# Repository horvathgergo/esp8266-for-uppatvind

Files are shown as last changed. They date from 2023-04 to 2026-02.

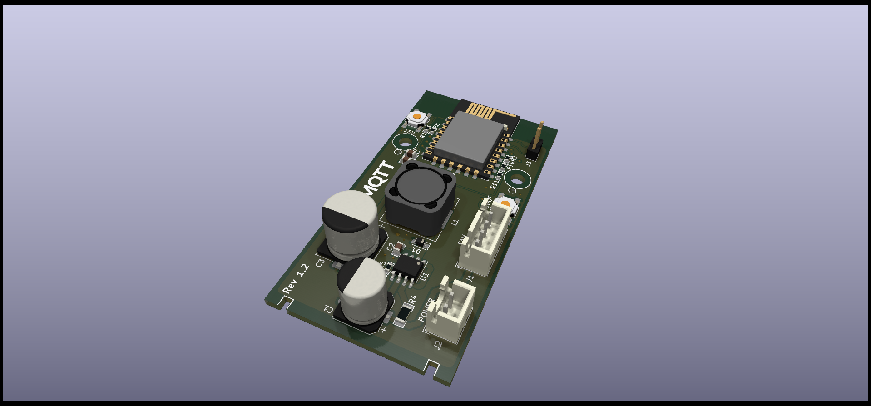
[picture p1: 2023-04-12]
Hardware/3D-model/3d-front2.png

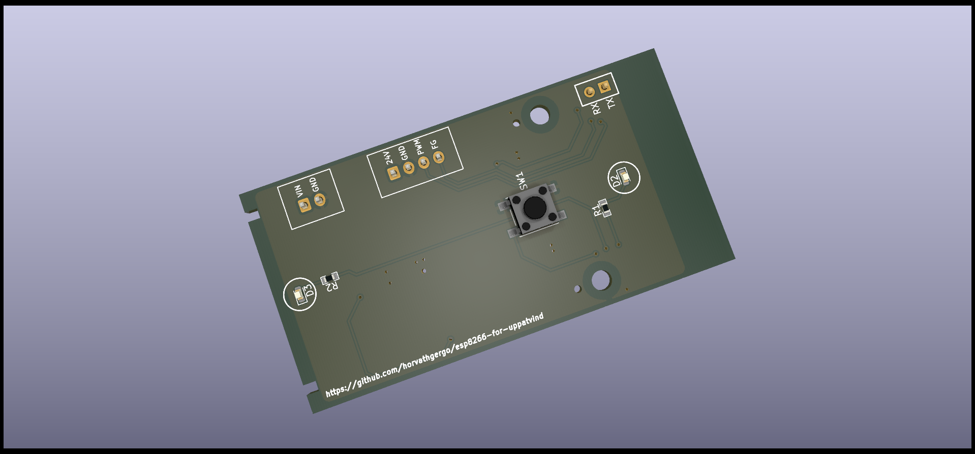
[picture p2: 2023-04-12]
Hardware/3D-model/3d-back.png

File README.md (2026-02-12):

# Smart Air Purifier (Project Uppåtvind)
Custom PCB based on ESP12-F (ESP8266) wifi module that serves as a smart controller for IKEA Uppåtvind Air Purifiers. It's embedded microcontroller enables you to incorporate your device to home automation systems (preferably to Home Assistant) or control it via custom mobile applications as it enjoys support from wide variety of firmwares. This project was implemented in two major phases. Hardware was designed with KiCAD, software is based on MicroPython.

About IKEA Uppåtvind: It is the newest air purifier of the swedish company, compact and even smaller than its older borther, Förnuftig. It effectively cleans the indoor air from harmful PM2.5 particles and pollen for cheap (price approx. EUR30). The device is optimised for small bedrooms and has three fan speed. 

Current status of the development: **Finalized**

Hardware: 
* [x] Schematic
* [x] Layout
* [x] BOM, CPL
* [x] 3D model 
* [x] Testing

Software:
* [X] MicroPython

## Hardware



PCB has the same size as the original one (70x36 mm) with mounting holes placed on it, thus it is supposed to fit just fine inside the plastic housing. Power supply of the fan is +24V, 0.8A. The board has a MC34063DR switching voltage regulator that provides the necessary power (+3v3, >500mA) for the wifi module. With the onboard physical button you can toggle the fan (turn on/off or even change speed). Two blue LEDs are connected to the ESP pins so it can indicate changes in operating mode. Note: to avoid unnecessary costs and save some space on the board physical filter reset button is not incorporated in this version as this function can be easily achieved through software side. 

The Purifier has a 4-pin PWM fan with +24VDC, 0.5A. The pins are POWER, GND, PWM, FG. PWM is a control pin for pulse width modulation and FG is the tacho pin for feedback purposes. The fan operates with a constant duty cycle of 50% and variable frequency between ca. 1-300Hz.

475CF212-3C40-45C2-A7EA-1FA76863B281

MCU programming: the board supports only UART programming via TX, RX pin headers (no USB interface), thus USB to TTL converter is necessary to upload firmware. It is recommended to supply the module via VIN and GND pins when programming. It is compatible with +5-24V supply (but +3V3 supply is not guaranteed to work as you may experience some voltage drop via the buck converter so make sure to provide enough voltage during flashing). Boot button is located on the right side of the wifi module.

BOM: Most of the chosen components are considered to be basic/standard parts at LCSC, however there are some extended components on the list (two large cap, inductor, esp, jst connectors and uart pin headers, tactile switch).

## Software

The software for Uppåtvind has been developed in Micropython. It enables the device to be controlled via mqtt while exploits Home Assistant mqtt autodiscovery features that provides with a smooth (almost zero config) setup process. 

More detailed description is available in this repo: https://github.com/horvathgergo/uPurifier

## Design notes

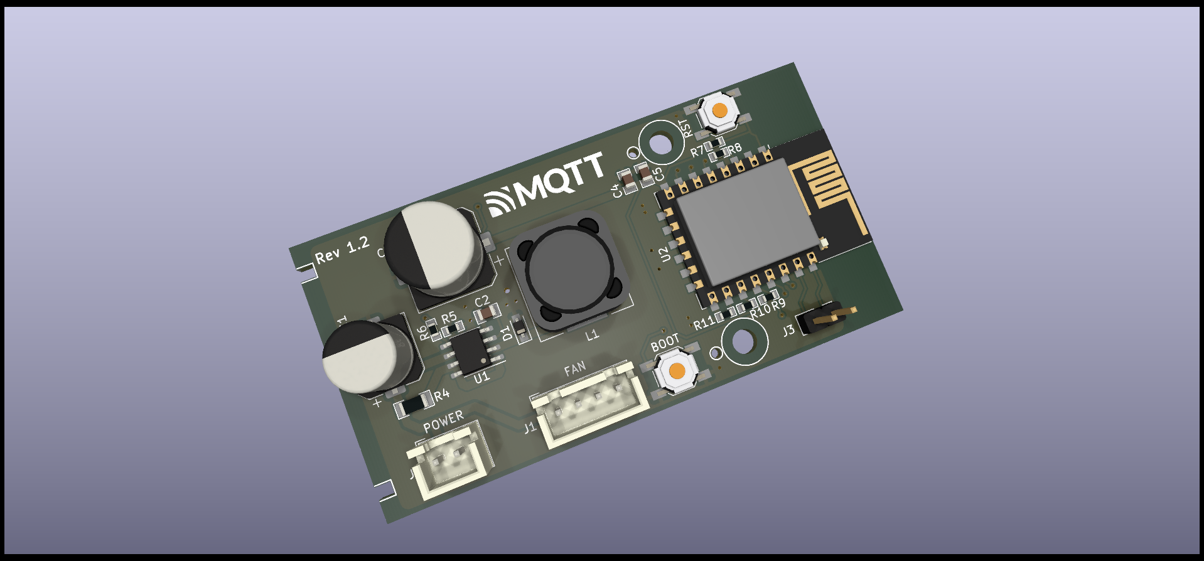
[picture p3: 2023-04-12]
Hardware/3D-model/3d-front.png

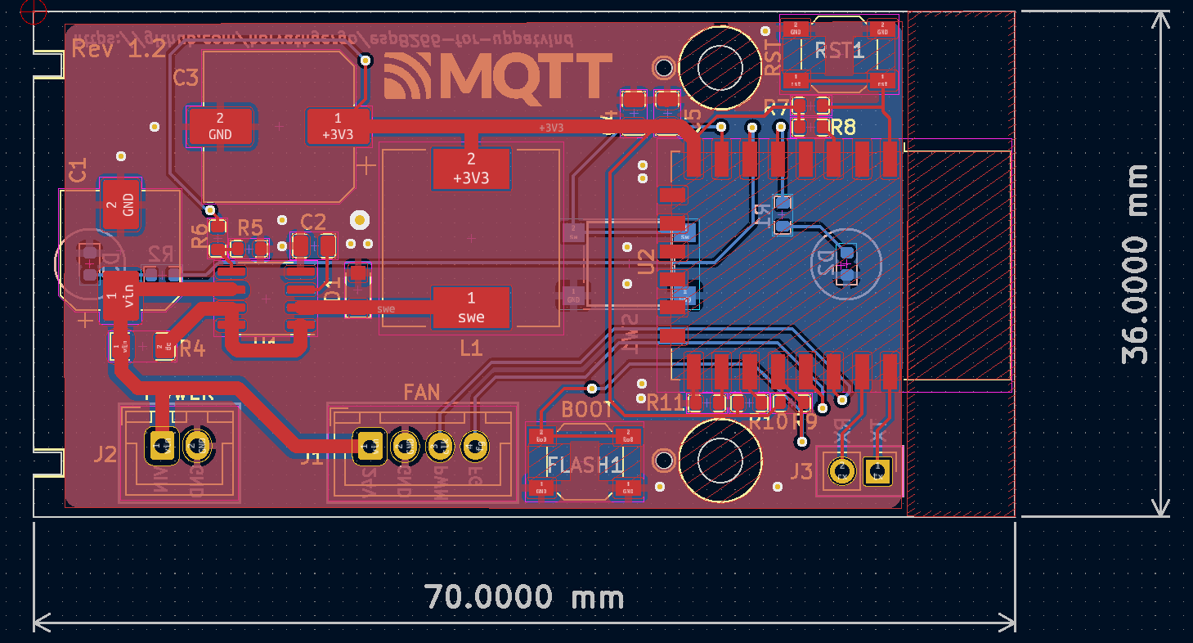
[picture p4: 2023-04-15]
Hardware/Air-Purifier-Uppatvind-Layout.png

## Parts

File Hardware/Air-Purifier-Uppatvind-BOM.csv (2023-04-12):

Comment | Designator | Footprint | LCSC Part Number
100uF | C1 | Capacitor_SMD:CP_Elec_8x10 | C445063
470pF | C2 | Capacitor_SMD_HG:C_0805_2012Metric_HG | C1743
470uF | C3 | Capacitor_SMD:CP_Elec_10x10.5 | C72518
10uF | C4 | Capacitor_SMD_HG:C_0805_2012Metric_HG | C15850
100nF | C5 | Capacitor_SMD_HG:C_0805_2012Metric_HG | C28233
D_Schottky | D1 | Diode_SMD:D_SOD-323_HandSoldering | C191023
LED | D2, D3 | LED_SMD:LED_0603_1608Metric | C72041
SW_Push | FLASH1, RST1 | SKQGABE010:SW_SPST_SKQG_WithStem | C318884
Fan | J1 | Connector_JST:JST_XH_B4B-XH-A_1x04_P2.50mm_Vertical | C144395
Power | J2 | Connector_JST:JST_XH_B2B-XH-A_1x02_P2.50mm_Vertical | C161869
UART | J3 | Connector_PinHeader_2.54mm:PinHeader_1x02_P2.54mm_Vertical
220uH | L1 | PSPHAQ127-221M:L_12x12mm_H8mm | C10151
120 | R1 | Resistor_SMD_HG:R_0603_1608Metric_HG | C22787
270 | R2 | Resistor_SMD_HG:R_0603_1608Metric_HG | C22966
0.15 | R4 | Resistor_SMD_HG:R_1206_3216Metric_Pad_HandSolder_HG | C247454
2K | R5 | Resistor_SMD_HG:R_0603_1608Metric_HG | C22975
3K3 | R6 | Resistor_SMD_HG:R_0603_1608Metric_HG | C22978
10K | R7, R8, R9, R10, R11 | Resistor_SMD_HG:R_0603_1608Metric_HG | C25804
SW_Push | SW1 | Tactile-Switch-6-6:SW_Push_1P1T_NO_6x6mm_H5mm | C255812
MC34063AD | U1 | MC34063:MC34063 | C32078
ESP-12F | U2 | RF_Module:ESP-12E | C82891

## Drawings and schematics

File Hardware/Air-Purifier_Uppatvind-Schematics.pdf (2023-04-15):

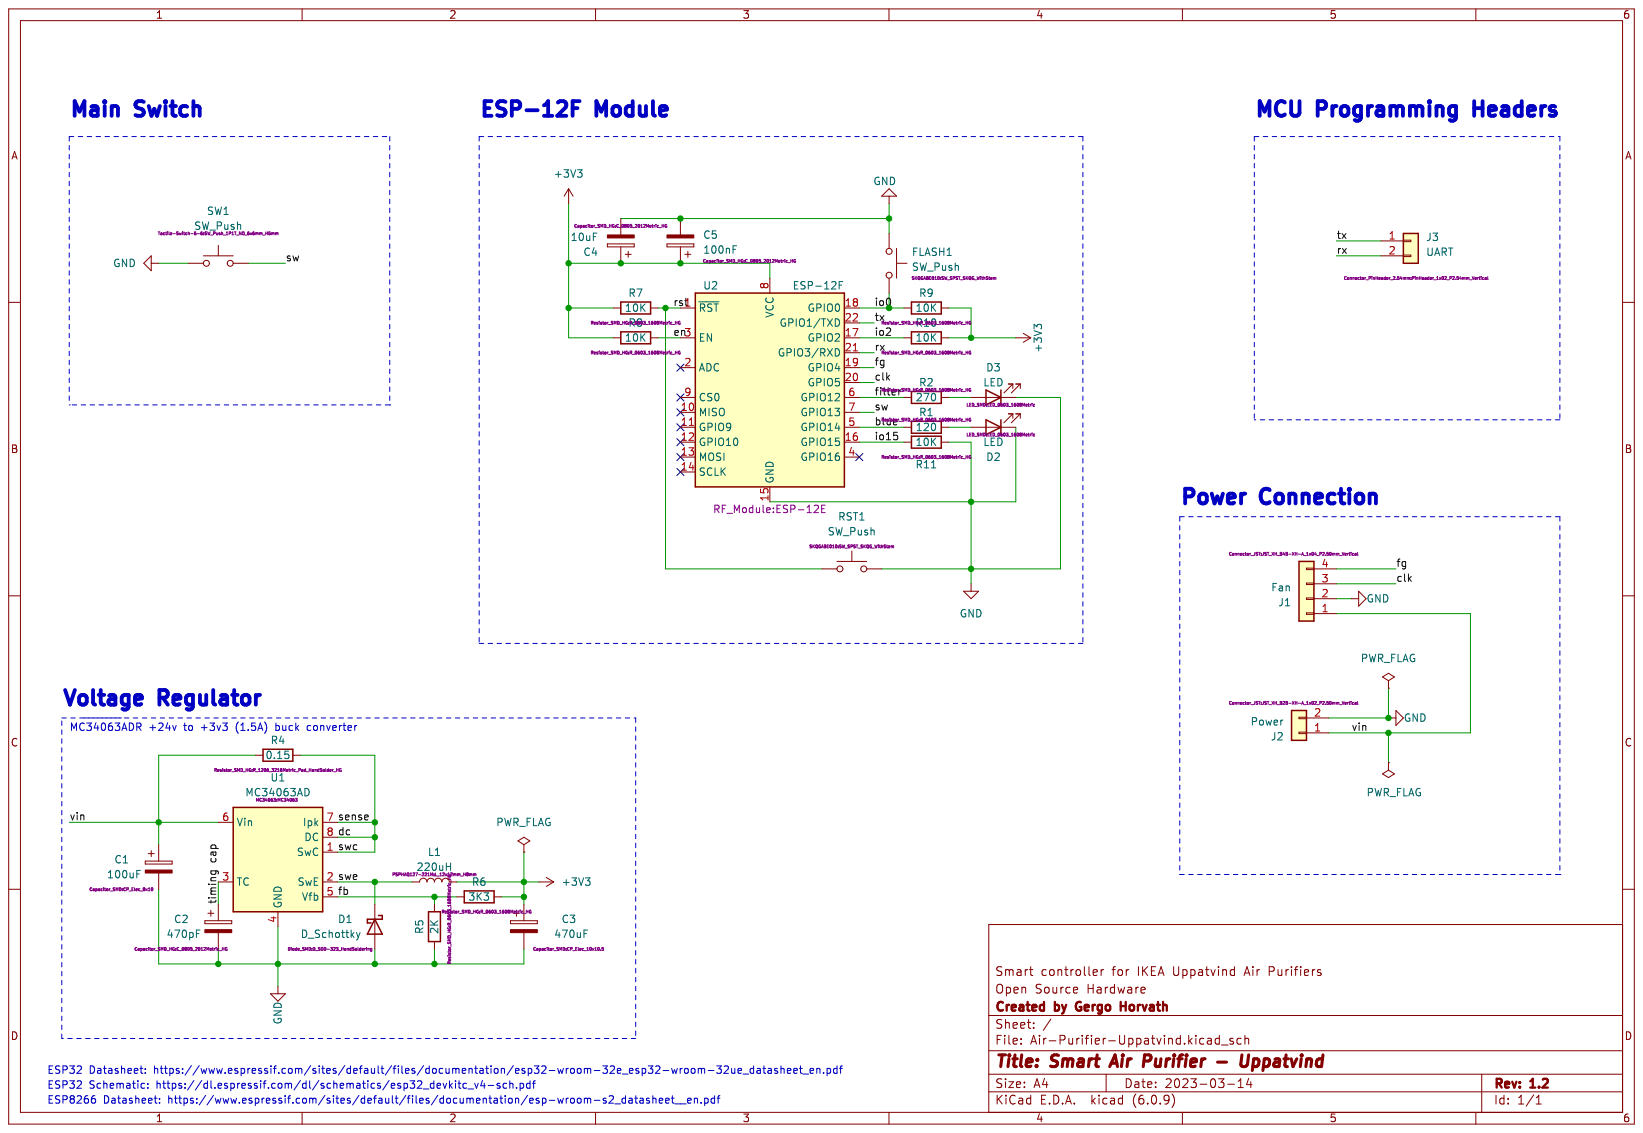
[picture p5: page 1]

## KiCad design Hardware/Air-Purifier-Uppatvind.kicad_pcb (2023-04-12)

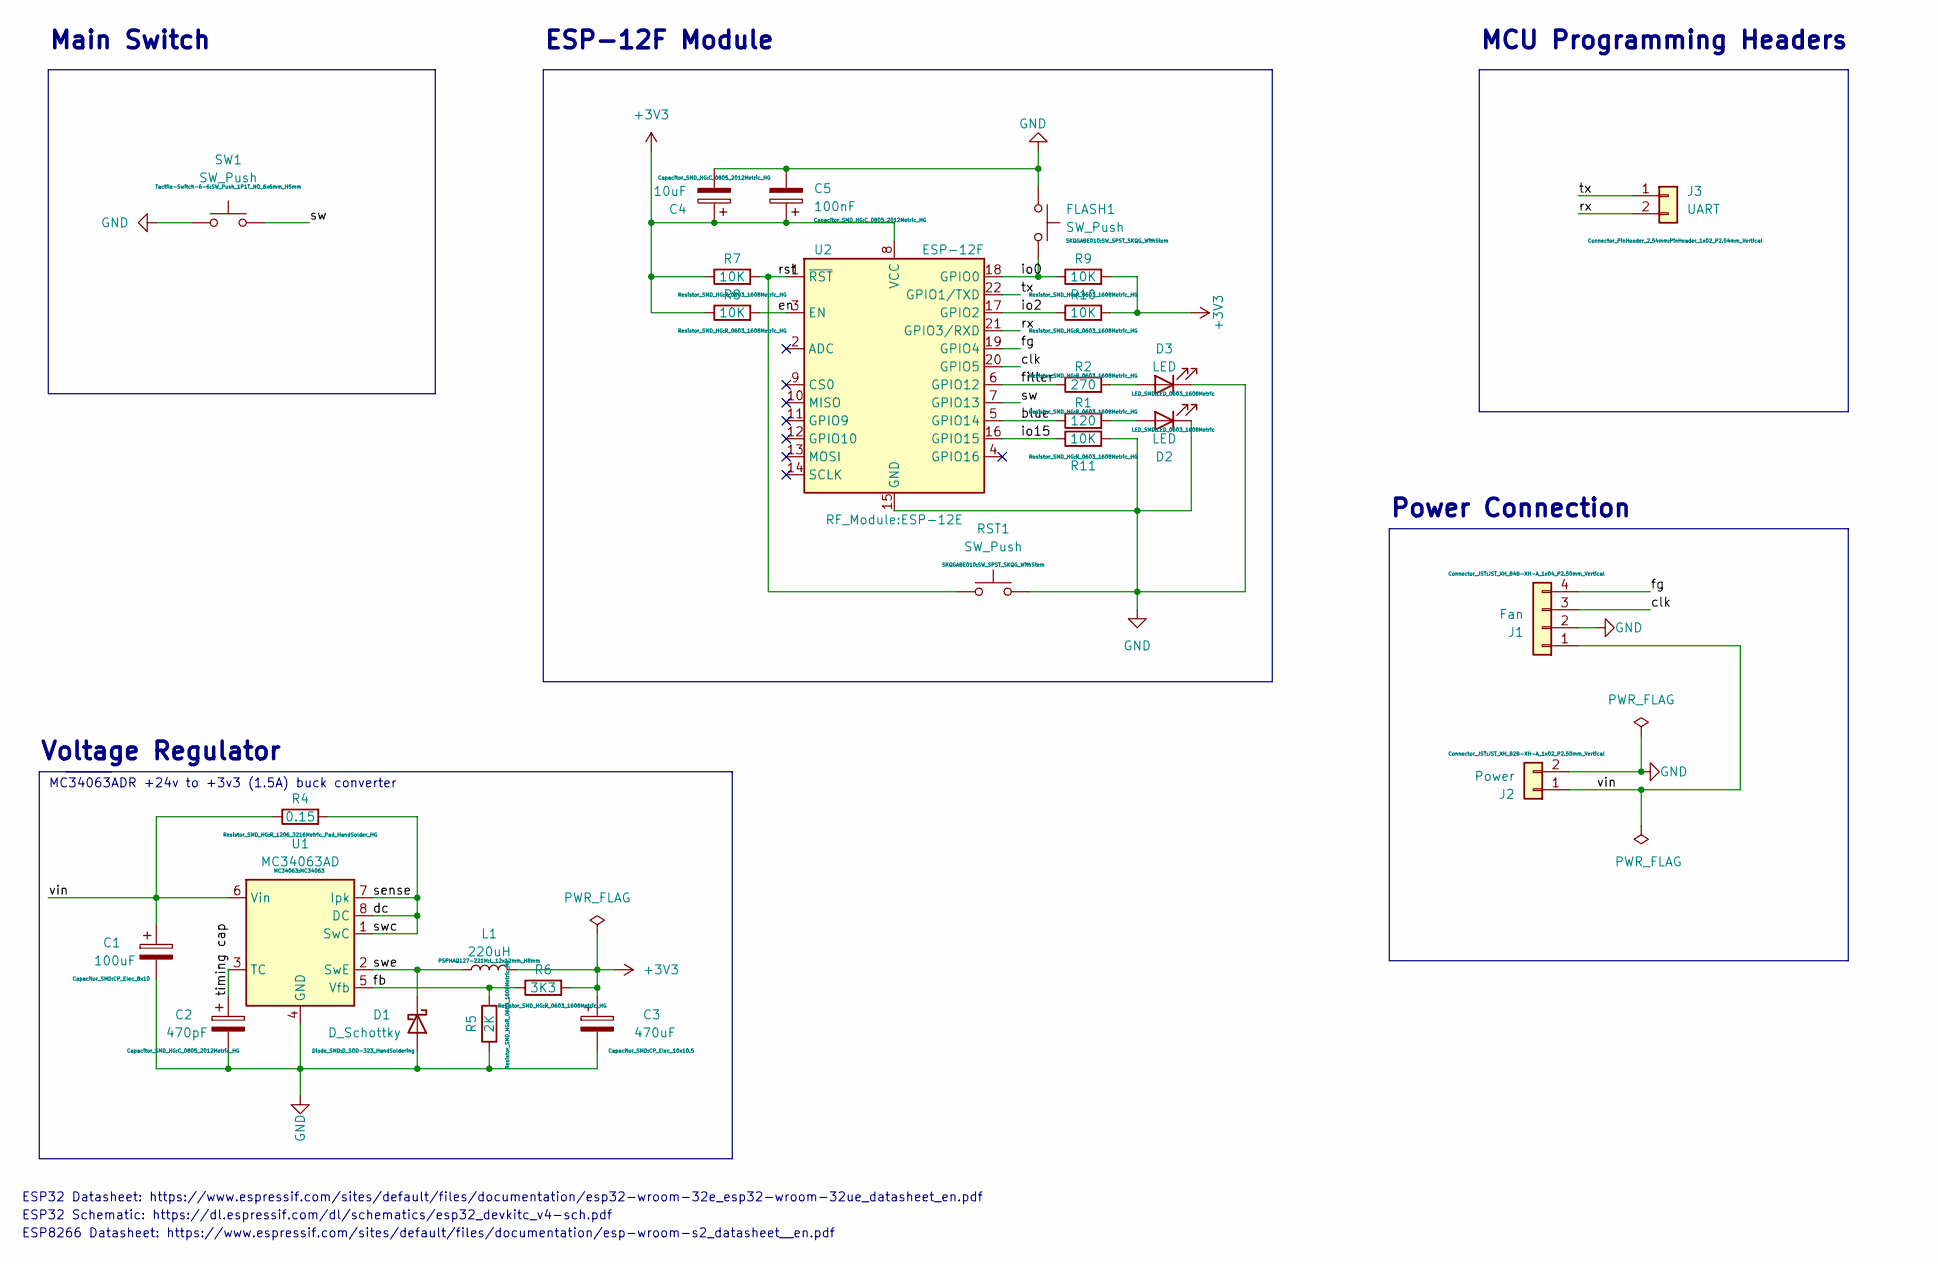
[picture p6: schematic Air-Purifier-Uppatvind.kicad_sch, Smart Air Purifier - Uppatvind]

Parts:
C1: 100uF; CP_Elec_8x10; LCSC C445063
C2: 470pF; C_0805_2012Metric_HG; LCSC C1743
C3: 470uF; CP_Elec_10x10.5; LCSC C72518
C4: 10uF; C_0805_2012Metric_HG; LCSC C15850
C5: 100nF; C_0805_2012Metric_HG; LCSC C28233
D1: D_Schottky; D_SOD-323_HandSoldering; LCSC C191023
D2, D3: LED; LED_0603_1608Metric; LCSC C72041
FLASH1: SW_Push; SW_SPST_SKQG_WithStem; LCSC C318884
J1: Fan; JST_XH_B4B-XH-A_1x04_P2.50mm_Vertical; LCSC C144395
J2: Power; JST_XH_B2B-XH-A_1x02_P2.50mm_Vertical; LCSC C161869
J3: UART; PinHeader_1x02_P2.54mm_Vertical
L1: 220uH; L_12x12mm_H8mm; LCSC C10151
R1: 120; R_0603_1608Metric_HG; LCSC C22787
R2: 270; R_0603_1608Metric_HG; LCSC C22966
R4: 0.15; R_1206_3216Metric_Pad_HandSolder_HG; LCSC C247454
R5: 2K; R_0603_1608Metric_HG; LCSC C22975
R6: 3K3; R_0603_1608Metric_HG; LCSC C22978
R7, R8, R9, R10, R11: 10K; R_0603_1608Metric_HG; LCSC C25804
RST1: SW_Push; SW_SPST_SKQG_WithStem; LCSC C318884
SW1: SW_Push; SW_Push_1P1T_NO_6x6mm_H5mm; LCSC C255812
U1: MC34063AD; MC34063; LCSC C32078
U2: ESP-12F; ESP-12E; LCSC C82891

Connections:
+3V3: C3.1, C4.1, C5.1, L1.2, R6.2, R7.1, R8.1, R9.2, R10.2, U2.8 (VCC)
/blue: R1.1, U2.5 (GPIO14)
/clk: J1.3, U2.20 (GPIO5)
/dc: R4.2, U1.1 (SwC), U1.7 (Ipk), U1.8 (DC)
/en: R8.2, U2.3 (EN)
/fb: R5.2, R6.1, U1.5 (Vfb)
/fg: J1.4, U2.19 (GPIO4)
/filter: R2.1, U2.6 (GPIO12)
/io0: FLASH1.2, R9.1, U2.18 (GPIO0)
/io2: R10.1, U2.17 (GPIO2)
/io15: R11.1, U2.16 (GPIO15)
/rst: R7.2, RST1.1, U2.1 (~RST)
/rx: J3.2, U2.21 (GPIO3/RXD)
/sw: SW1.2, U2.7 (GPIO13)
/swe: D1.1 (K), L1.1, U1.2 (SwE)
/timing cap: C2.1, U1.3 (TC)
/tx: J3.1, U2.22 (GPIO1/TXD)
/vin: C1.1, J1.1, J2.1, R4.1, U1.6 (Vin)
GND: C1.2, C2.2, C3.2, C4.2, C5.2, D1.2 (A), D2.1 (K), D3.1 (K), FLASH1.1, J1.2, J2.2, R5.1, R11.2, RST1.2, SW1.1, U1.4 (GND), U2.15 (GND)
unnamed: D2.2 (A), R1.2
unnamed: D3.2 (A), R2.2

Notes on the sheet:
MC34063ADR +24v to +3v3 (1.5A) buck converter
ESP32 Schematic: https://dl.espressif.com/dl/schematics/esp32_devkitc_v4-sch.pdf
ESP-12F Module
Voltage Regulator
Power Connection
MCU Programming Headers
ESP8266 Datasheet: https://www.espressif.com/sites/default/files/documentation/esp-wroom-s2_datasheet__en.pdf
ESP32 Datasheet: https://www.espressif.com/sites/default/files/documentation/esp32-wroom-32e_esp32-wroom-32ue_datasheet_en.pdf
Main Switch

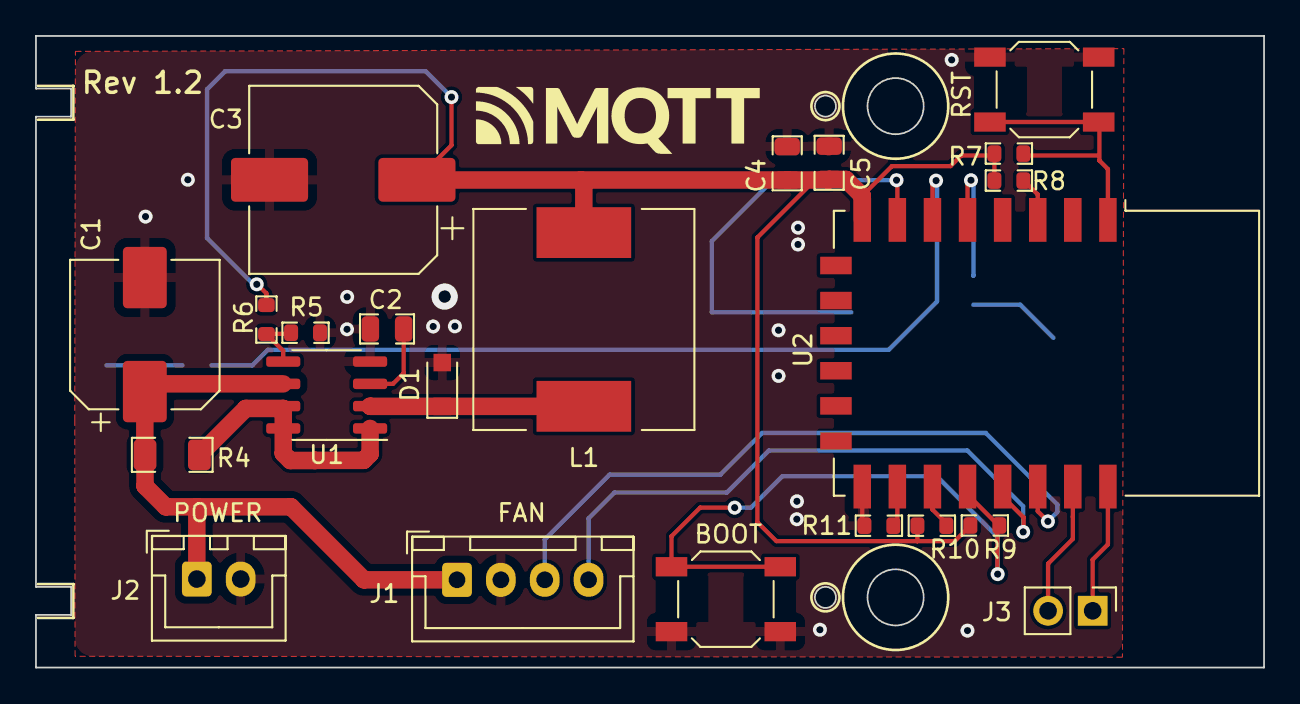
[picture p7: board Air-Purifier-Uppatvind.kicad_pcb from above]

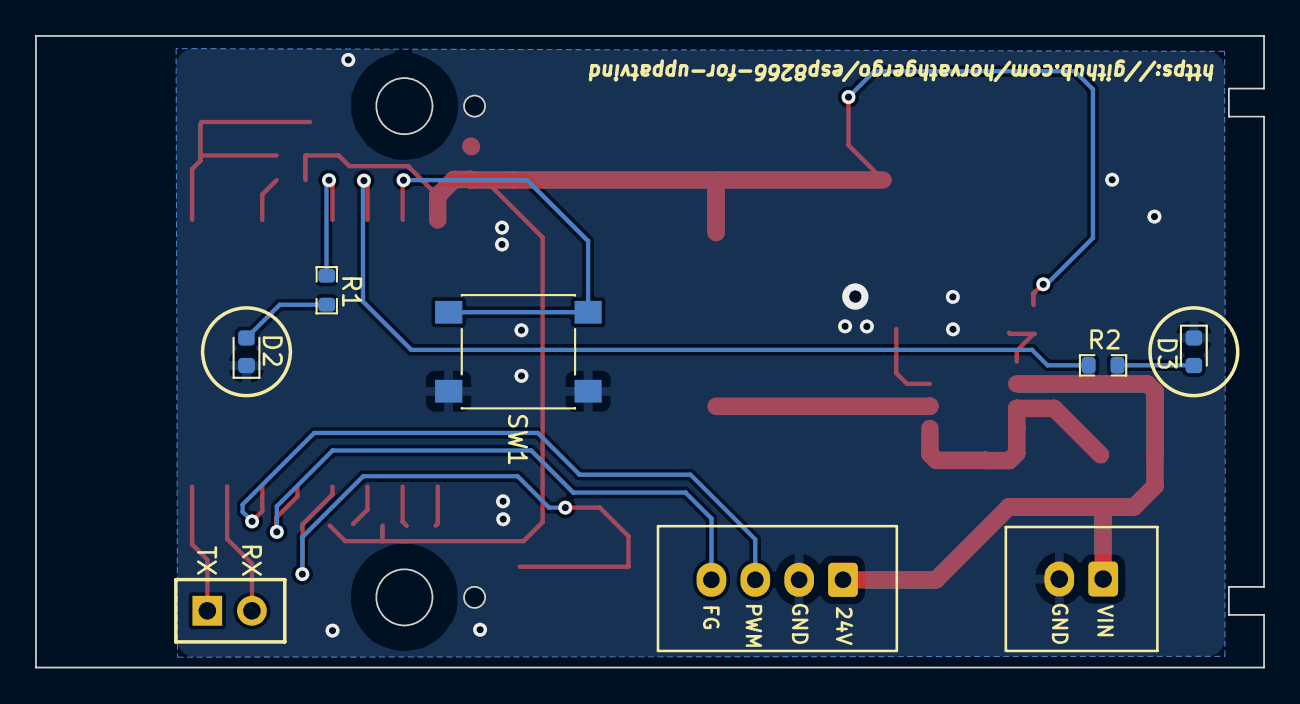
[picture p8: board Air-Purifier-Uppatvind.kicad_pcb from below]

Board: 2 copper layers, 70.0 x 36.0 mm, 27 parts (5 on the bottom side), 21 nets.

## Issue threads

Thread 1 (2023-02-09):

Status and Questions

seniorm0ment, 2023-02-09:
Hello, I am very interested in what you are doing.
I was curious roughly how long until you could say it is a stable product to use? Few months?
Roughly how much could one expect to pay, and how easy is it to install? Just a few solder points?

And I presume it won't monitor/track anything about how much its filtering, or when a filter is due, or the current air quality? Or am I wrong?

Curiously have you attempted to use a smart switch to turn the filter on and off for the time being? I don't have the filter yet, but I was curious if shutting it off via the switch will allow it to automatically come back on, or if you still need to press the button.

horvathgergo, 2023-02-10:
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

Hi! Thanks for your interest in this project. I assume it's not going to take months if everything goes as expected.🙃 However, in order to optimize the development costs I ordered the PCB tailored only for Fornuftig (basically the same as Uppatvind with some differences in physical control). So I will test the source code on it first and only after then create a modified version for Uppatvind.

I can confirm that the original purifier remembers the last state so you can control it with a smart plug too. But in this case you will not be able to change speed via HA and I think it won't be a much cheaper solution than this PCB. I don't have an exact number in mind but I assume to be around EUR8-10 each. Note: the pure board is super cheap as production is nowadays available from $2/5pcs. Further costs include components, shipping and assembly. Final price mainly depends on if you can solder it for yourself or make it assembled by a manufacturer. 😄

As for extra features, i have only bad news for you. For now, it's not on my list, but I open for ideas

seniorm0ment, 2023-02-11:
Awesome to hear buddy, appreciate your efforts. I look forward to seeing the future.

So you will be releasing a PCB for Fornuftig and Uppatvind?

Also as far as features I personally think would be cool, it would be cool to see a built in sensor or addon module that can give reports on what it filters or how the current air quality looks. But I understand that is not a priority, just my suggestion :)
Keep up the good work, the community appreciates your effort. Thanks.

Raapale, 2023-09-23:
Hi, great project! I have a basic question about the fan in Uppåtvind device: What voltage range does the fan motor operate with? Is the fan speed adjusted with just changing the voltage? I'm wondering if I can operate the fan directly by just feeding it with 12V power at my solar panel cottage (bypass/disconnect device's own control equipment and power inlet)....

horvathgergo, 2023-09-23:
If you just feed the motor with 24v or 12v then it won't work. You should adjust the PWM frequency via CLK pin

Johnellegon, 2024-07-01:
Where would I go about ordering a board, don't know where to begin.  (Complete newbie)

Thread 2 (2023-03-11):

Motor control pin is not PWM

maxmacstn, 2023-03-11:
Hello,

I just bought the IKEA UPPATVIND, and have a similar idea that adding Wi-Fi to this cheap air purifier would be a good idea.

After checking the output signal from the control board using an oscilloscope, I found out that the motor speed controller is not PWM (pulse width modulation) signal. The duty cycle remains the same at 50% on every speed setting, but frequency changes.

The signal probed at TP9 has the logic level of 5V and the frequency are:

| Speed                   | Frequency (Approx.)  |
|------------------|----------------------|
| Off                         | 0V                            |
| I                             | 124Hz                          |
| II                            | 198Hz                          |
| III                           | 257Hz                          |

Moreover, the controller board also cuts off 24V power while in the off state.

I see that this project is currently in the testing stage and I think you might have a controlling problem if you use only the PWM signal.

Hope you find this information useful.

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

horvathgergo, 2023-03-11:
Hi [maxmacstn](https://github.com/maxmacstn)! Thanks for your great feedback! You are absolutely right, the duty cycle of the fan is constant and you can control the speed by changing its frequency (a bit misleading from IKEA that they literally call it PWM though 😄). TBH I didn't check the exact freqs of the original module as you did, only the current which is approx. 70mA for speed I., 160mA for speed II. and 320mA for speed III.

If you check the code of the micropython firmware (here: https://github.com/horvathgergo/uPurifier) that I wrote to both Fornuftig and Uppatvind, you can see that I set duty cycle to zero only if I turn off the fan. For speed I, II, III the duty is 50% with variable frequency between 1-300Hz. I've tested it and it works perfectly so there is no need to cut the 24v power off. Anyway I may consider lowering the maximum frequency as it can challenge the limits of the fan.

maxmacstn, 2023-03-12:
Hi,

I haven't seen that you have already figured out and already wrote the firmware for it. Nice!

This repository is very useful and I will use the information here as a reference for my design. I think I will use an ESP32 (for supporting Matter protocol), add colour LEDs, or even a built-in PMS dust sensor.

Thank you very much.👍

Closed 2023-03-12.

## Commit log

2022-12-31 Update README.md
    Initialize PCBHome logo
2023-01-28 Added BOM file
    [BOM.csv]
2023-01-28 Added CPL files
    [CPL_bottom.csv, CPL_top.csv]
2023-01-28 Added Schematic v1.0
2023-01-28 Added Gerber
2023-01-28 Added CPL file
    [CPL.xlsx]
2023-01-28 BOM update
    [BOM.csv]
2023-01-29 Add v1.1 files
    [BOM.csv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]
2023-04-12 Added files (board v1.2)
    [Air-Purifier-Uppatvind-BOM.csv, Air-Purifier-Uppatvind.kicad_pcb, Air-Purifier-Uppatvind.kicad_sch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]
2023-04-15 Added Schematics and Layout (board v1.2)
